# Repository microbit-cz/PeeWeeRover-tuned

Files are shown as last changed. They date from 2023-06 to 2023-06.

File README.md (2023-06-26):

# PeeWee robocar



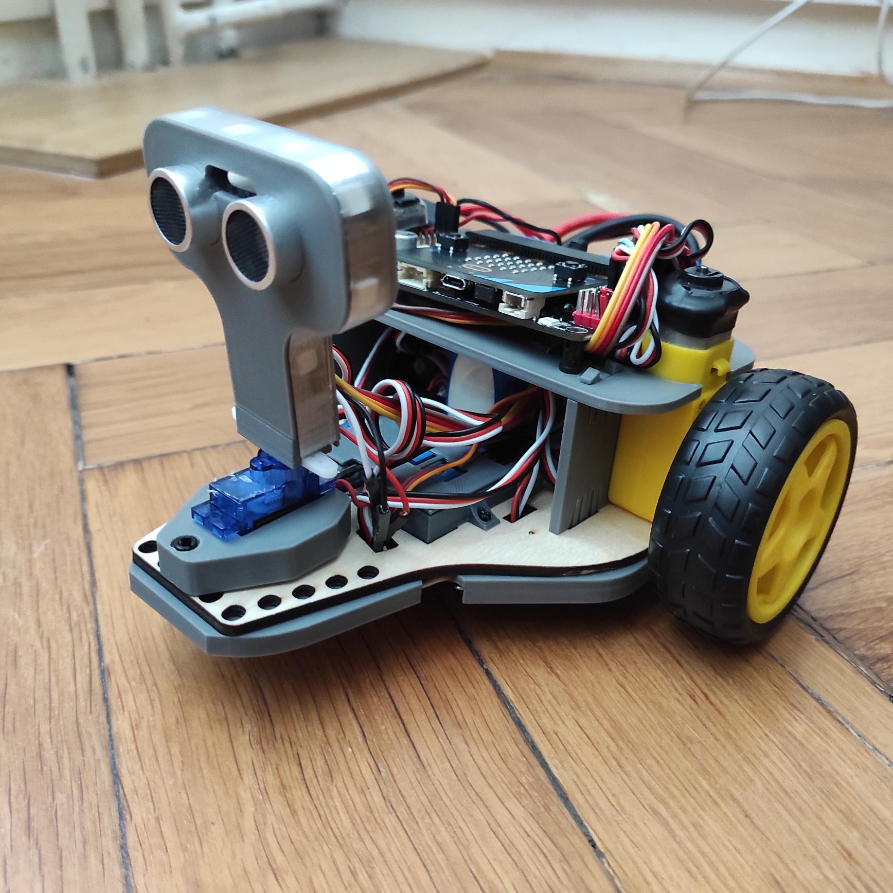
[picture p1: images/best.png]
PeeWee whole


The PeeWee RoboCar can be printed from home and programmed using a Micro:bit.
Thanks to the printable parts, you don't have to worry, because you can print the cart yourself.

## Price
The price can vary greatly depending on the import,
but after adding up the prices in the table above, the price is <b>~79.65 USD.</b>.

However, this price does not include filament from printing, engraving, screws, etc.

## Components
Components purchased | Price
--- | ---
[Lithium battery](https://www.lipolbaterie.cz/103-lipol-lipo-baterie-turnigy-3s-2200mah-20c-11-1v.html)| 24.14 USD
[2x Motor](https://www.specialni-naradi.cz/motorek-3-6v/0-17a-s-prevodovkou-prevod-1/48)| 5.63 USD
[3x IR sensor](https://www.laskakit.cz/arduino-ir-opticky-infra-snimac-fc-51/)| 3.88 USD
[2x IR wheel sensor]([./](https://www.makerstore.com.au/product/robo-sensor-speed/))| 6.00 USD
[LED strip](https://www.mall.cz/led-pasky/ledsoft-ws2812b-led-pasek-18w-m-ip20-100084347241) | 8.09 USD
[Engine:Bit](https://www.aliexpress.com/i/4000834837807.html)| 31.72 USD
[Lego plugs](https://www.malekostky.cz/Lego-Technic-pin-cerny-sada-10ks-d2803.htm)| 0.09 USD

Components printed |
--- |
[2x LED holder side](./sorce/Side_LED_holder.SLDPRT/) |
[LED holder front](./source/Front_LED_holder.SLDPRT) |
[LED holder middle](./source/Middle_LED_holder.SLDPRT) |
[Sensor box](#) |
[Sensor Cover](#) |
[2x Sidewalls](./source/Side_holder.SLDPRT) |
[Battery holder](#) |

Engraved components |
--- |
[Motherboard](./sorce/Mother_board.SLDPRT)|

## Preparation of components
### 3D Printing
1. Download the files -
Download from **./printfiles** folder, here you will find file **All.std** .
2. The print itself -
Open the **All.std** file in an optional 3D printing application.
Printing should take around 5h 30min.
3. Removing the parts -
Remove the individual parts from the print surface and clean the battery holder from the supports.

### 4. Motherboard
Unlike the other components, the base plate is made of plywood, so it is necessary to engrave it.
1. Download the file **./pieces/MotherBoard**
2. Open the file you downloaded in your optional engraving program
3. Let it be engraved
4. Engraving can take approximately 3 hours 30 minutes
5. Remove the plywood you have engraved

## Build
1. Check that this opening is on the left side

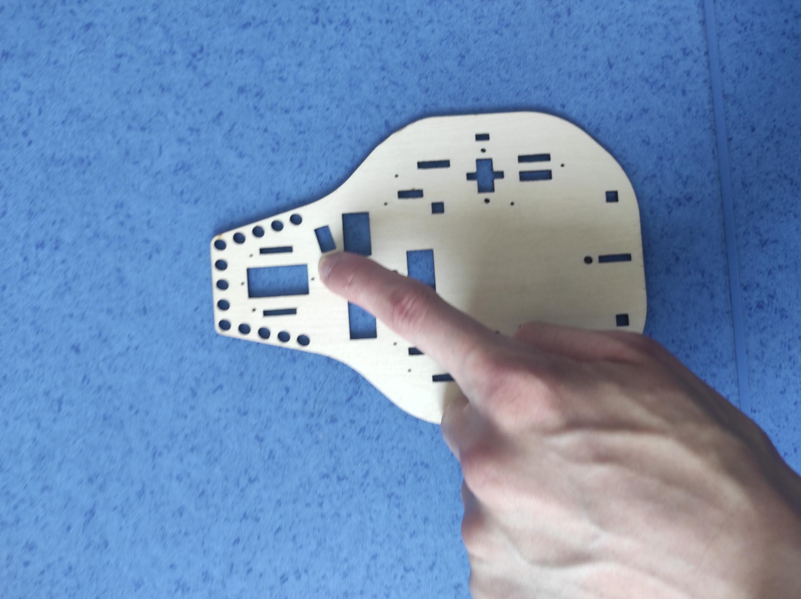
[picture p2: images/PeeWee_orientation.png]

<br>

### 1. LED holder
Take the individual LED holders and place their screw holes over the holes in the main board as shown.
Place a screw with a diameter of approx. M2.2x6.5 in each hole as shown in the picture.
Screw each LED holder with a screw.

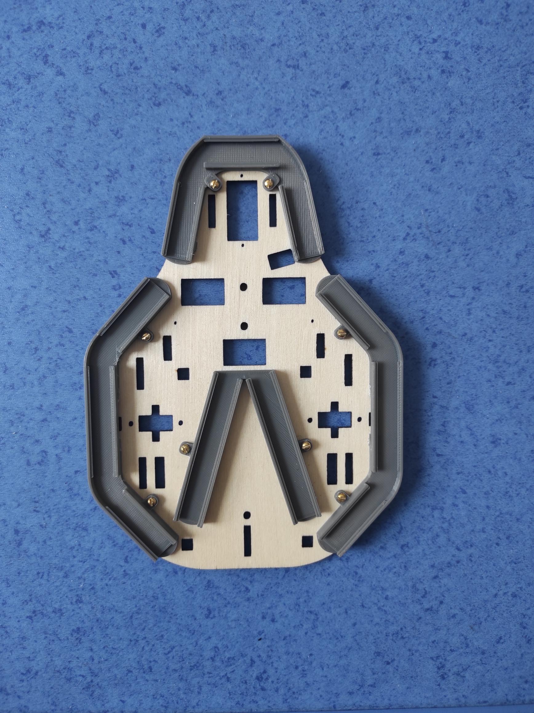
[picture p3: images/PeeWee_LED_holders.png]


### 2. Soldering the LED
Cut your LED strip as follows:
* 2 x 3 LEDs
* 7x 2 LEDs
* 2 x 4 LEDs
Mount and solder as shown

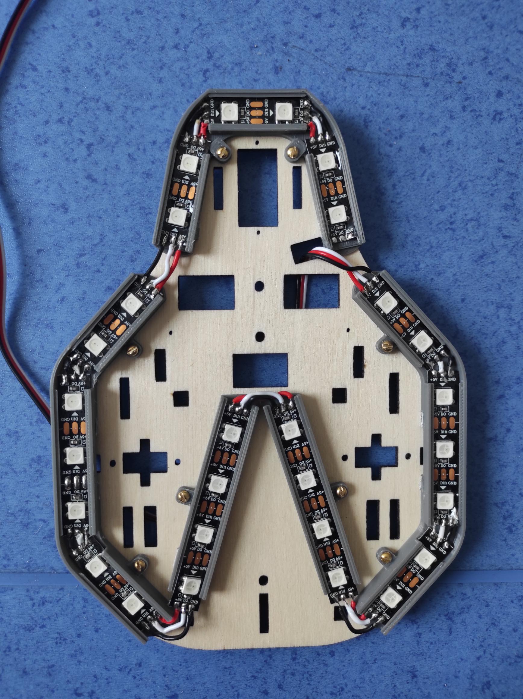
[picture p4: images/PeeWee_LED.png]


### 3. Bottom wheels for holding
1. Put M3x8 screws in 2 holes at the top, put a steel ball at the bottom and fix with a nut
2. Do for both balls
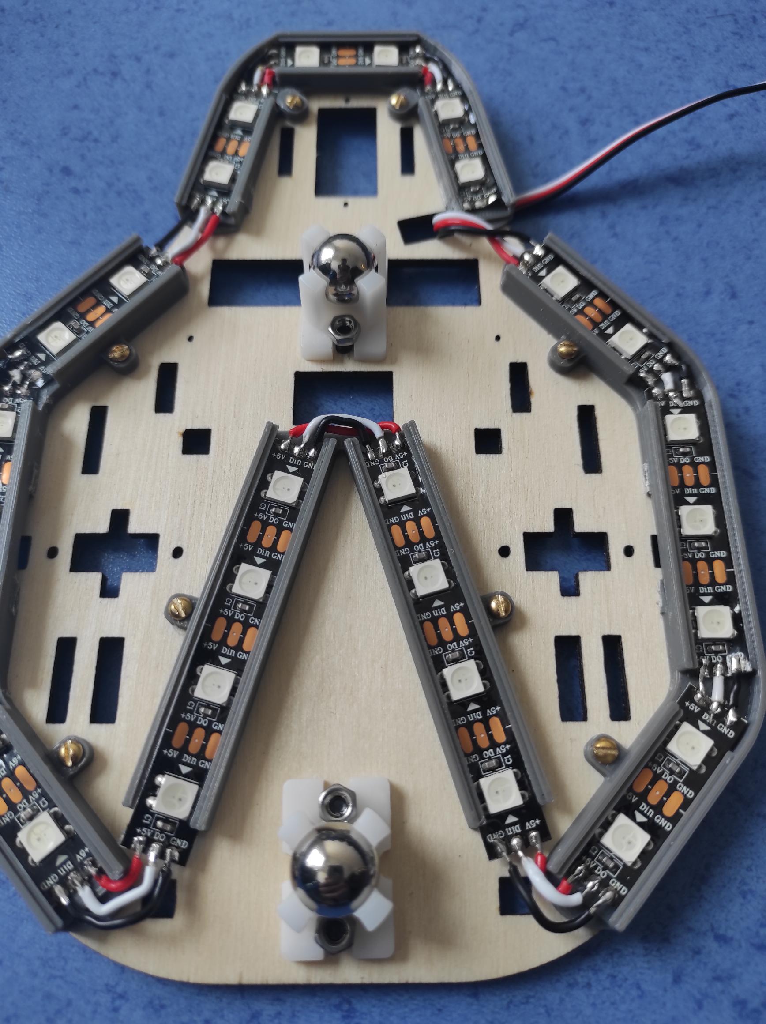
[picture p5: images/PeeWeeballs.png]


### 4. IR box
1. place the IR box in these three holes
2. Screw the IR box to the board using two M1.7x4 screws
3. Insert the IR sensors into the box.
4. Snap on the top cover.
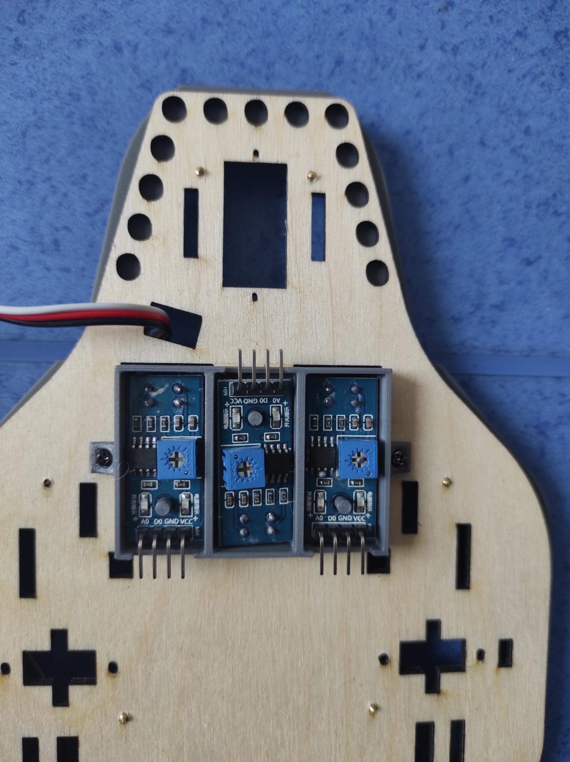
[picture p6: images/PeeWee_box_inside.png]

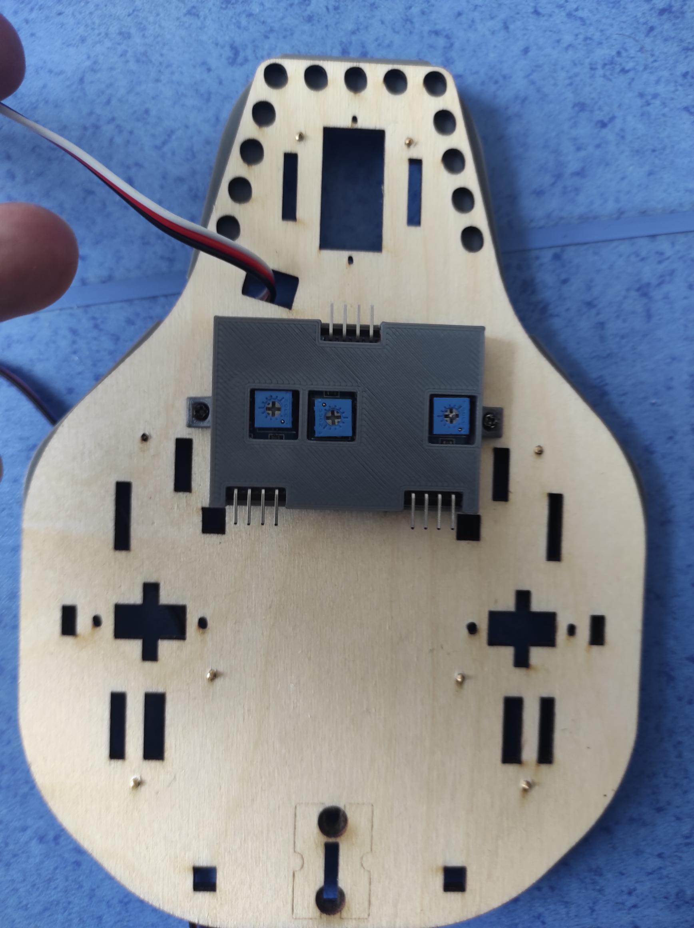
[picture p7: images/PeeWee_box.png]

### 5. Engines
1. Fix the IR sensors for measuring rotation from below with M2.5x8 screws
2. Snap both sides into the wooden board
3. Insert the motors into the base plate from below and screw M3x8 screws into the side
4. Attach the plastic wheel to the motor rod
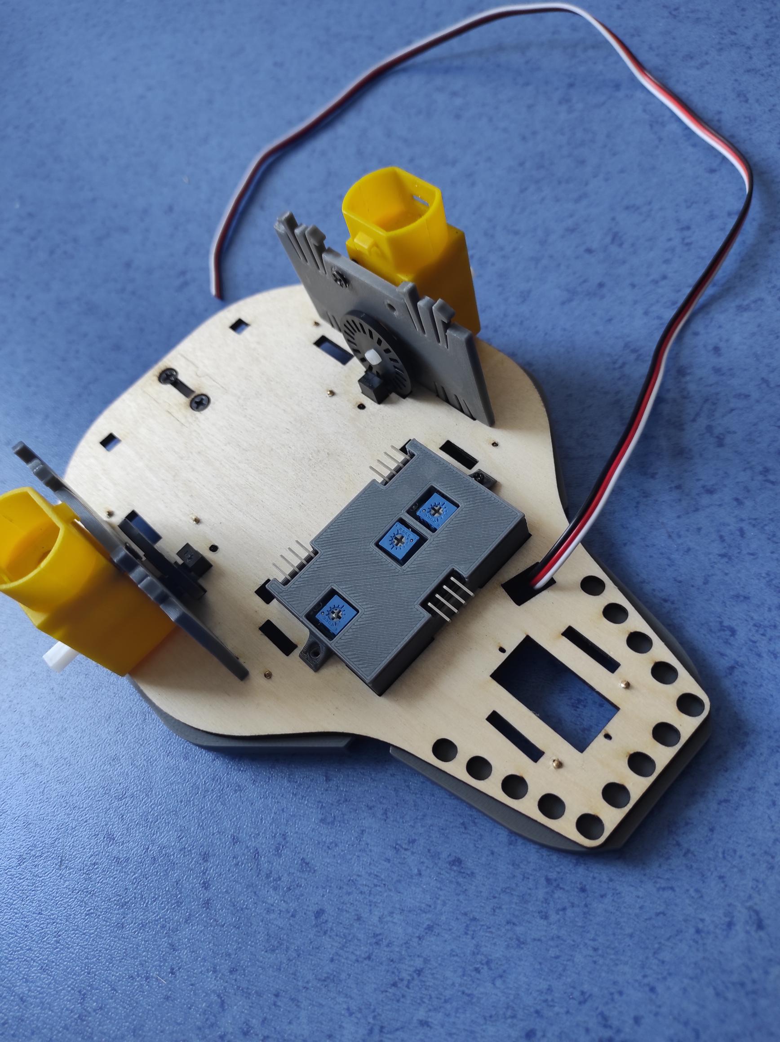
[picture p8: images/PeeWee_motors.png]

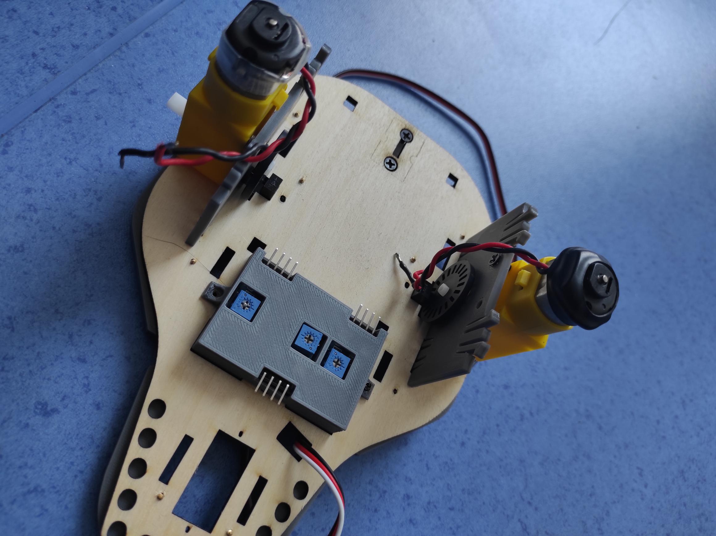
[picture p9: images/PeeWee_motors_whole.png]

6. Finally, snap the top panel to the sides
   
### 6. Engagement
Take the Motor:Bit and place it on the top panel using the lego plugs.<br>
Disconnect as follows:
Part of | Pin
--- | ---
Left engine | M1
Right engine | M4
Left IR Sensor | P14
Mid IR Sensor | P15
Right IR Sensor | P13
Left wheel encoder | P12
Right wheel encoder | P8
LEDs | P0
   
### 7. Testing
1. Upload this code to your microbit
2. Insert your Micro:Bit into the Motor:Bit

Note: If the cart behaves differently, you must have made a mistake somewhere, so check the cart according to the previous part of the manual.
## Motorbit V2.0
[Tutorial for coding](https://github.com/emakefun/pxt-motorbit)

## Author
[@LukasChaloupecky](https://github.com/LukasChaloupecky)

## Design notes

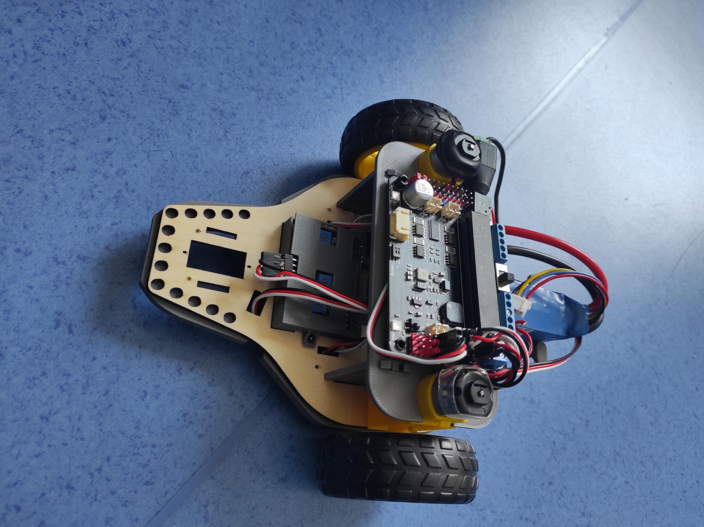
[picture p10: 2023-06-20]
images/PeeWee.png

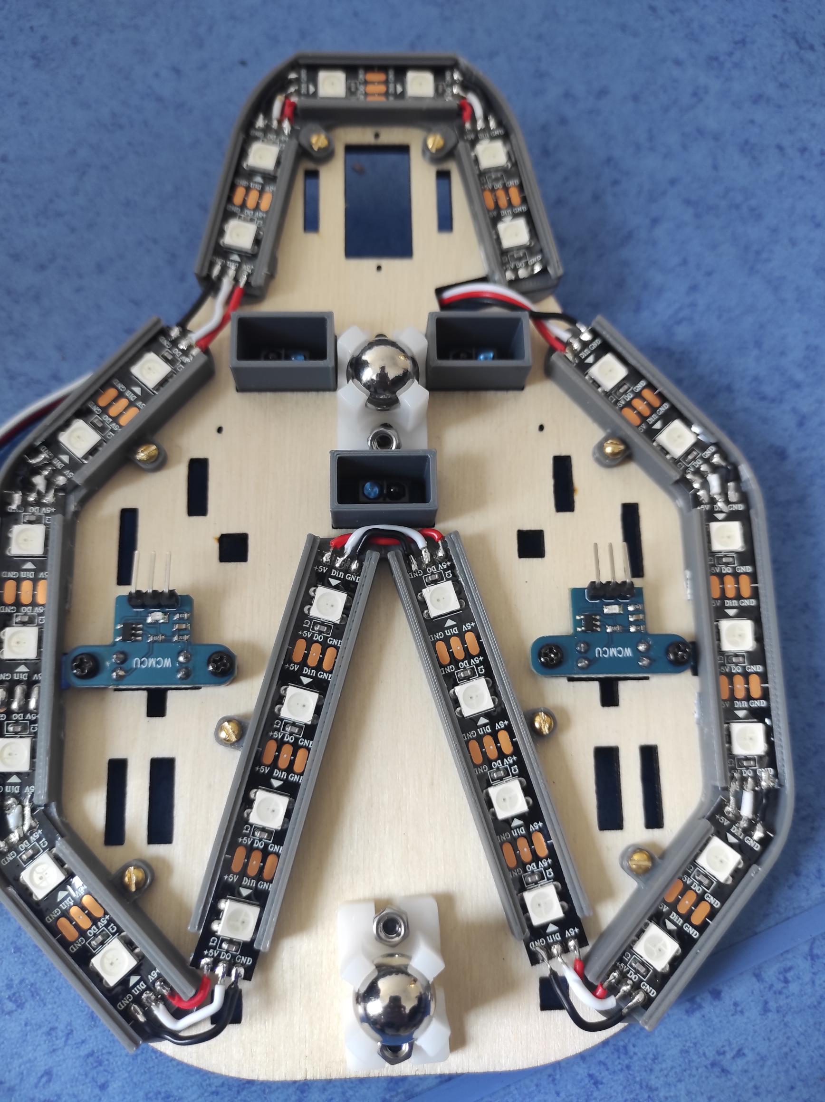
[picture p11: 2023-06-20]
images/PeeWee_IR_bottom.png

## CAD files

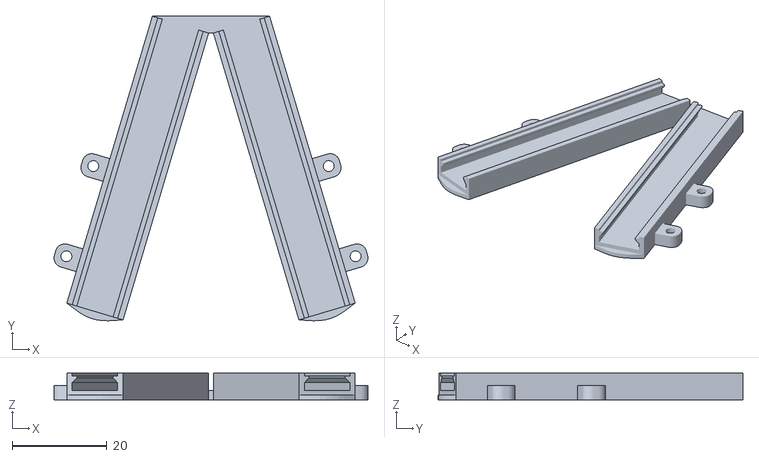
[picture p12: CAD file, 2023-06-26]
PRINT/A_led díl_down.STL
66.3 x 64.3 x 5.60

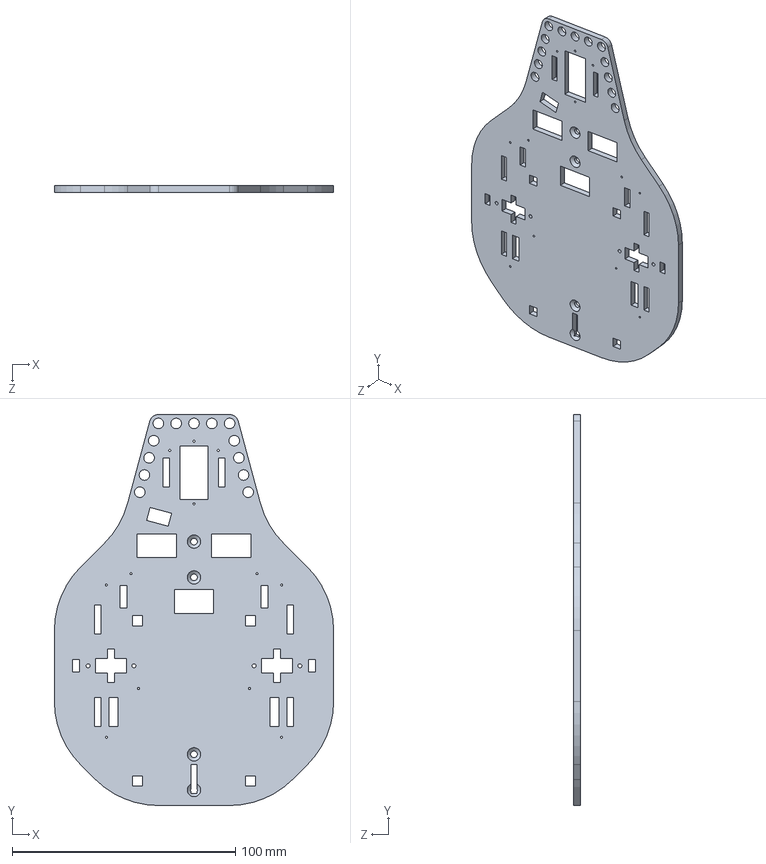
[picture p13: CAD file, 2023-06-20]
source/Mother_board.SLDPRT
125.0 x 175.0 x 3.00 mm

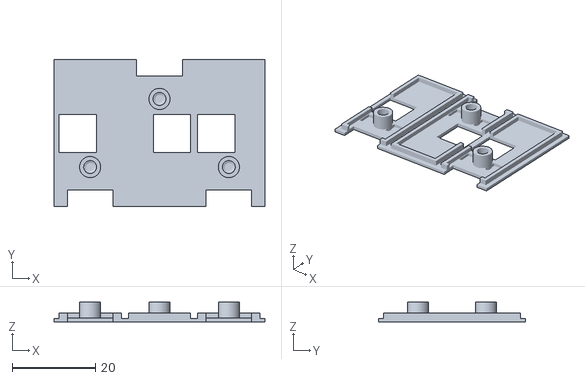
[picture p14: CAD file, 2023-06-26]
PRINT/PeeWee-IR_lid.STL
50.8 x 35.4 x 4.80

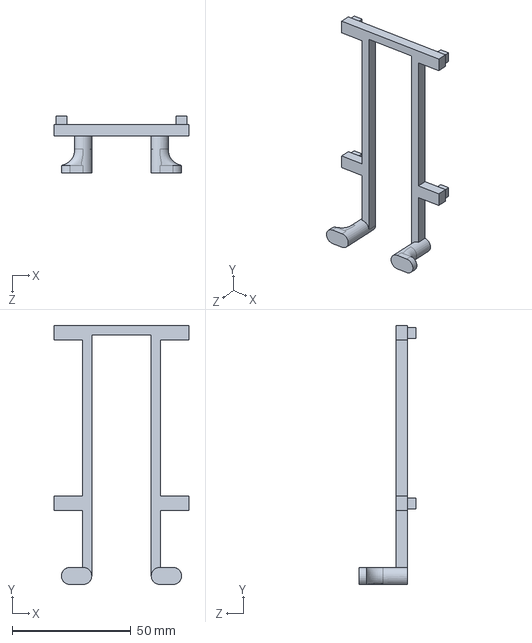
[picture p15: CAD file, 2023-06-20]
source/baterie_lower.SLDPRT
56.8 x 109.0 x 23.8 mm

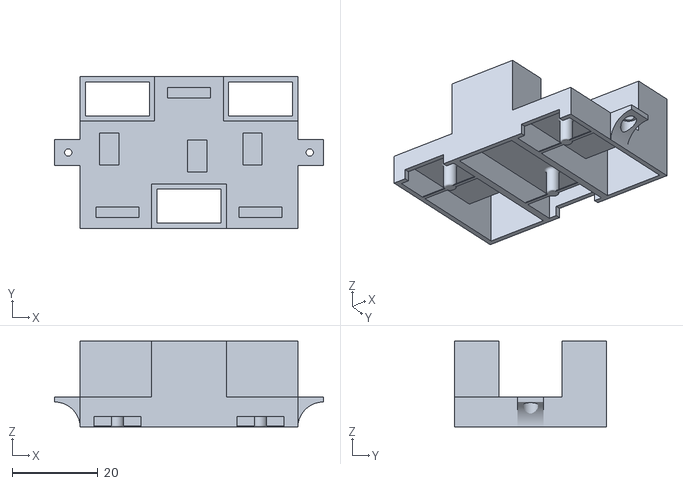
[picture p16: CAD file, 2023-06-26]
PRINT/PeeWee-IR_box.STL
62.8 x 35.4 x 20.0

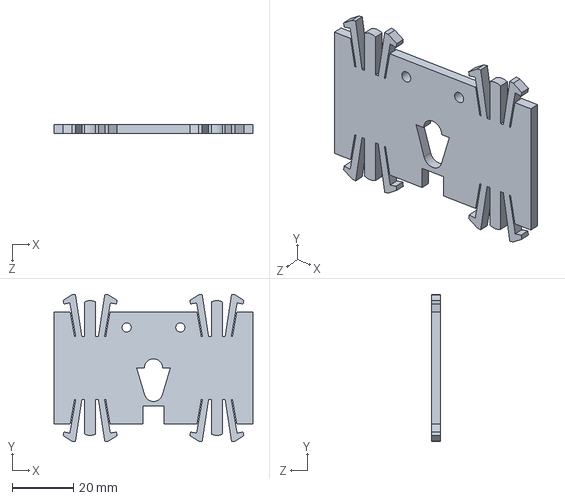
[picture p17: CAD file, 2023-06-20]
source/Side_holder.SLDPRT
65.0 x 48.2 x 2.80 mm

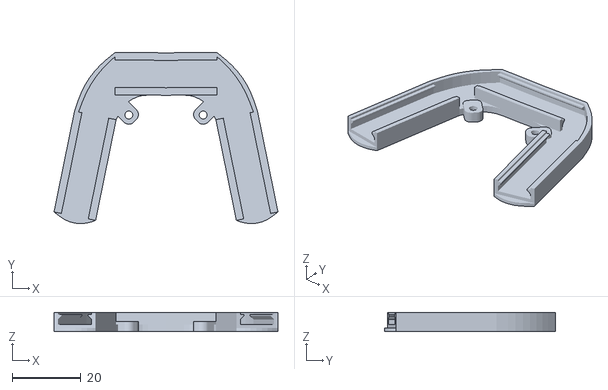
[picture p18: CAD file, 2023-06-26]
PRINT/horni_LED_holder.STL
65.4 x 50.0 x 5.60

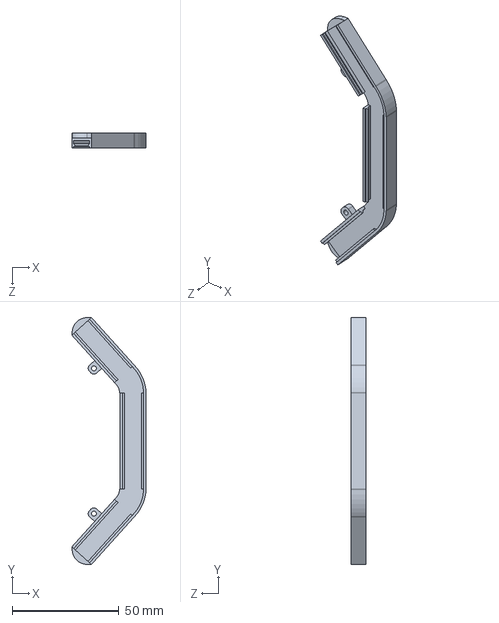
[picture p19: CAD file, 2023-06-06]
source/Side_LED_holder.SLDPRT
34.9 x 115.9 x 7.00 mm

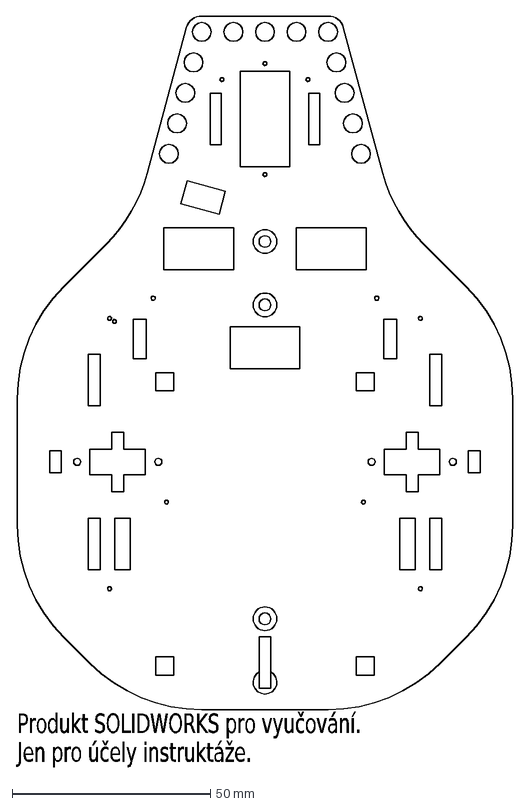
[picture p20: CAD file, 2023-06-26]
PRINT/well_ (2).DXF
Produkt SOLIDWORKS pro vyučování.
Jen pro účely instruktáže.

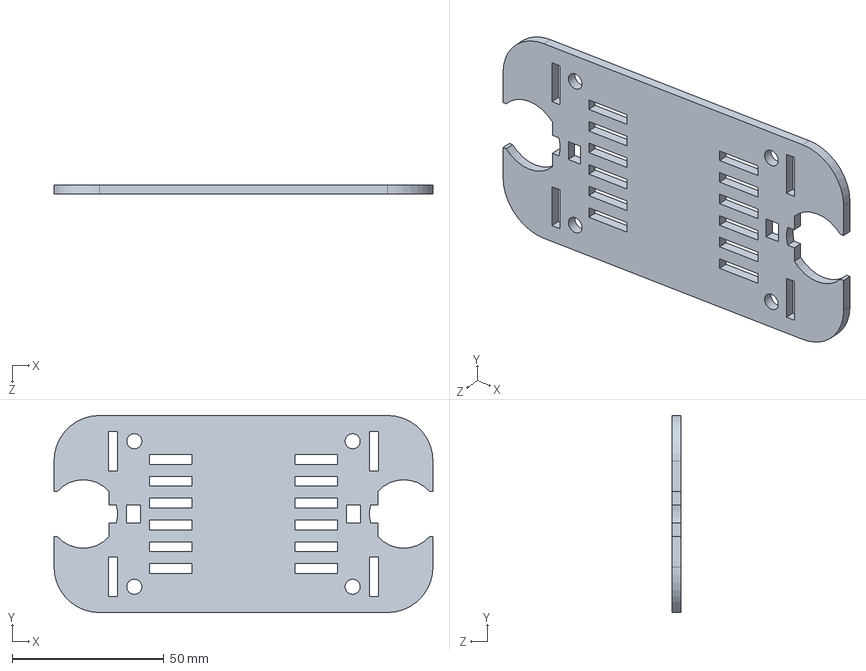
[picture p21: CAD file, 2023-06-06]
source/Top-panel.SLDPRT
125.0 x 65.0 x 3.00 mm

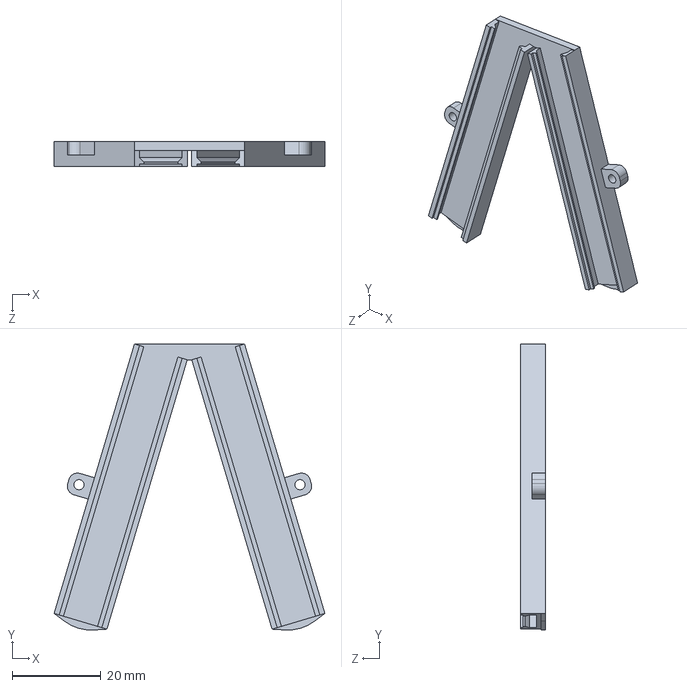
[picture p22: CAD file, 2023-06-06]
source/Middle_LED_holder.SLDPRT
60.9 x 64.3 x 5.60 mm

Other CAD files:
PRINT/vnejsi LED_holder.STL
PRINT/PeeWee-Top-magic_bit_ s dírami ve středu.STL
source/Front_LED_holder.SLDPRT
PRINT/PeeWee-connectors_lock.STL
PRINT/baterie_lower.STL

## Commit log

2023-05-16 Dilek do stredu na led
    [strad_led_finaleSLDPRT.SLDPRT]
2023-05-16 Sestava_vytahnout z ni dilky na LED
    [sestava_23_50.SLDASM]
2023-05-17 oprava
    Tsik, 2x vnejši led holder, 1 stredni (bud delsi nebo kratsi drzaky) a 1 predni led holder A jednou top s opravenými dírami
2023-05-17 Add files via upload
    Přidane kraje na led hold.
